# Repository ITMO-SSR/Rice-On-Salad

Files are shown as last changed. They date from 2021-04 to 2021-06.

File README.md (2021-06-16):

[English](README_EN.md)
# Rice-On-Salad
**Цель проекта:**
Разработать доступный для воспроизведения проект гусеничной платформы с возможностью удаленного управления через ПК 
и ориентации в пространстве через камеры.
****
**Описание:**
Полностью Open-Source проект с возможностью легкого повторения. Все детали для печати будут лежать в открытом доступе.
****
**Задачи проекта:**
- Разработать и собрать гусеничную платформу
- Подобрать необходимую электронику
- Реализовать удаленное управление платформой через ПК и смартфон
- Добавить автоматическое управление
****
**Желаемый результат:**
Получить полностью управляемую и самостоятельно ориентирующуюся в пространстве гусеничную платформу

***
# Установка ROS на Raspberry Pi
В данном разделе мы опишем процесс установки ROS на Raspberry Pi, а также расскажем о том, как подключить робота 
к своему компьютеру.

## Шаг 1.
Для работы Raspberry Pi требуется операционная система, которая хранится на карте microSD. 
В нашем проекте мы используем образ Ubuntu 16.04 с уже установленным ROS, 
который вы можете скачать по [ссылке](https://downloads.ubiquityrobotics.com/pi.html). 
Для записи образа на SD-карту вам потребуется программа [balenaEtcher](https://www.balena.io/etcher/).

## Шаг 2.
Для дальнейшей работы с Raspberry Pi вам нужно установить и настроить ROS на компьютере, 
с которого вы планируете подключаться к вашему роботу. 
Наиболее простой вариант — запустить образ Ubuntu с предустановленным ROS с помощью виртуальной машины.
1. Скачайте виртуальную машину [VirtualBox](https://www.virtualbox.org/wiki/Downloads) и установите её.
2. Скачайте образ Ubuntu по [ссылке](https://downloads.ubiquityrobotics.com/vm.html).
3. Разархивируйте файл, который вы скачали. В результате получится папка, внутри которой будет файл 
   с расширением `.vbox`. Запустите его. В результате откроется менеджер Virtual Box.
4. Проверьте параметры виртуальной машины и запустите её. Имя пользователя - `ubuntu`, пароль - `ubuntu`.

## Шаг 3.
Теперь, когда все необходимое ПО было установлено, рассмотрим процесс подключения к Raspberry Pi через SSH.
1. При первом включении Raspberry будет работать в режиме точки доступа Wi-Fi, к которой нужно будет подключиться 
   с вашего компьютера. Имя сети — `ubiquityrobotXXXX`, где `XXXX` - комбинация цифр. 
   Пароль для подключения - `robotseverywhere`.
2. После подключения к сети, откройте терминал в Ubuntu и введите команду `ssh ubuntu@10.42.0.1`. 
   Далее введите пароль `ubuntu`.
3. Для того чтобы в дальнейшем подключаться к роботу через вашу Wi-Fi сеть, нужно добавить её в список робота. 
   Для просмотра доступных сетей наберите команду `pifi list seen`. Для добавления вашей сети воспользуйтесь 
   командой `sudo pifi add MyNetwork password`, где `MyNetwork` и `password` - имя и пароль вашей сети. 
   Далее, введите `sudo reboot` в терминале. Это приведет к перезапуску робота, который теперь 
   будет автоматически подключаться к вашей сети.
4. Подключитесь к данной сети с вашего компьютера и снова откройте терминал Ubuntu. Теперь, чтобы подключиться к роботу, 
   воспользуйтесь командой `ssh ubuntu@address`, где `address` - IP-адрес вашего робота. Чтобы узнать его, 
   выполните следующие действия:
    1. Введите в терминале команду `ifconfig`. В ответ вы получите информацию по сетевым интерфейсам:
       
         ```
         eth0: flags=4099<UP,BROADCAST,MULTICAST>  mtu 1500
                 ether b8:27:eb:5b:d7:ae  txqueuelen 1000  (Ethernet)
                 RX packets 0  bytes 0 (0.0 B)
                 RX errors 0  dropped 0  overruns 0  frame 0
                 TX packets 0  bytes 0 (0.0 B)
                 TX errors 0  dropped 0 overruns 0  carrier 0  collisions 0
 
         lo: flags=73<UP,LOOPBACK,RUNNING>  mtu 65536
                 inet 127.0.0.1  netmask 255.0.0.0
                 inet6 ::1  prefixlen 128  scopeid 0x10<host>
                 loop  txqueuelen 1000  (Local Loopback)
                 RX packets 0  bytes 0 (0.0 B)
                 RX errors 0  dropped 0  overruns 0  frame 0
                 TX packets 0  bytes 0 (0.0 B)
                 TX errors 0  dropped 0 overruns 0  carrier 0  collisions 0
 
         wlan0: flags=4163<UP,BROADCAST,RUNNING,MULTICAST>  mtu 1500
                 inet 192.168.1.2  netmask 255.255.255.0  broadcast 192.168.1.255
                 inet6 fe80::1e3a:e952:1094:4fda  prefixlen 64  scopeid 0x20<link>
                 ether 00:e0:4c:06:6f:dc  txqueuelen 1000  (Ethernet)
                 RX packets 257  bytes 33734 (32.9 KiB)
                 RX errors 0  dropped 14  overruns 0  frame 0
                 TX packets 153  bytes 26653 (26.0 KiB)
                 TX errors 0  dropped 0 overruns 0  carrier 0  collisions 0
         ```           
       
       Обратите внимание на адрес `inet 192.168.1.2.`. IP-адрес Raspberry Pi будет иметь вид `192.168.1.x`, 
       где `x` - число от 1 до 255.
    2. Теперь, для того, чтобы найти адрес Raspberry Pi, можно воспользоваться 
       приложением [Advanced IP Scanner](https://www.advanced-ip-scanner.com). 
       Запустите приложение, введите `192.168.1.1-255` и нажмите "Сканировать". 
       В результате вы увидите список устройств, подключенных к вашей сети, среди которых будет и Raspberry.
5. Поздравляем! Вы подключились к своему роботу!

## Шаг 4.
Вполне вероятно, что в будущем вы захотите запускать часть нод на роботе, а часть на компьютере. 
Для этого настроим переменные среды.
1. Запустите виртуальную машину, откройте терминал и наберите следующие команды:
   
    ```
    echo "export ROS_MASTER_URI=http://<robot_ip>:11311" >> ~/.bashrc
    echo "export ROS_IP=$<workstation_ip>" >> ~/.bashrc
    ```
   
    где `<robot_ip>` и `<workstation_ip>` - IP-адреса робота и виртуальной машины соответственно.
2. Подключитесь к Raspberry Pi через SSH и наберите следующие команды:
   
    ```
    echo "export ROS_MASTER_URI=http://<robot_ip>:11311" >> ~/.bashrc
    echo "export ROS_IP=$<robot_ip>" >> ~/.bashrc
    ```

***
# Подключение шаговых двигателей к Arduino Uno с помощью CNC Shield
В данном разделе мы рассмотрим подключение шаговых двигателей к Arduino Uno, рассмотрим необходимые для этого 
компоненты и напишем небольшую тестовую программу.

## 1. Необходимые компоненты
1. CNC Shield v3.0
2. Arduino Uno
3. Драйверы A4988 - 2 шт.
4. Шаговые двигатели NEMA17 17HS4401 - 2 шт.
5. Шлейфы из 4 проводов для подключения шаговых двигателей - 2 шт.
6. USB-кабель для связи с компьютером

## 2. Соединение CNC Shield с Arduino Uno и драйверами
CNC Shield имеет четыре слота — для подключения четырех драйверов двигателей. Слоты, обозначенные желтым цветом, 
отвечают за оси X, Y, Z, красный слот — за ось A.

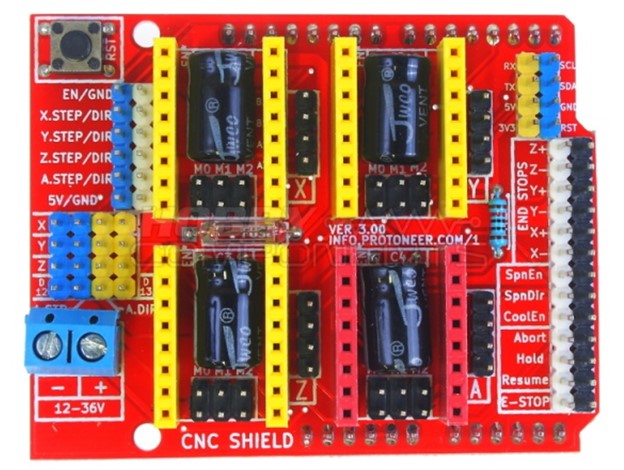
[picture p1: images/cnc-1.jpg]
CNC Shield 1


Ось A может дублировать одну из осей X, Y, Z с помощью дополнительного двигателя и драйвера. То есть входной сигнал 
приходит одинаковый, а драйверы и шаговые двигатели разные, но двигаются одинаково. В нашем случае 
дублирование осей не нужно, поэтому вставляем драйверы в 2 из 3 слотов X, Y, Z, а сам CNC Shield в Arduino Uno, 
как на картинке ниже.

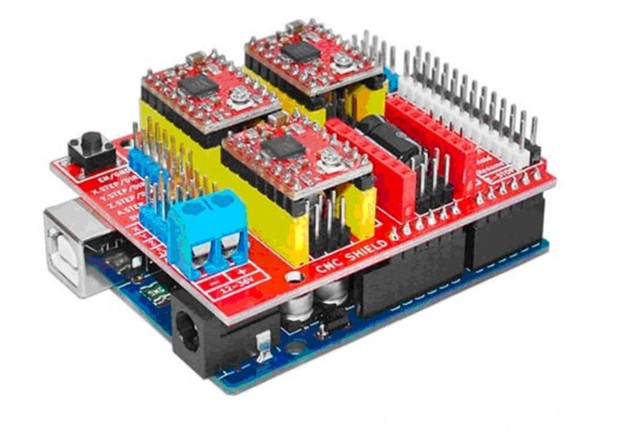
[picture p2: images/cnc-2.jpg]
CNC Shield 2


## 3. Настройка тока драйверов
Для настройки дополнительно потребуются отвертка и мультиметр.

Сначала подключим сборку плат к компьютеру по USB. Далее, включаем на мультиметре измерение постоянного напряжения 
напротив положения “20”. Для измерения напряжения необходимо приложить минусовой щуп к минусу на CNC Shield, 
а положительный щуп замкнуть с подстроечным резистором, который по совместительству является "+" в данной схеме. 
Необходимо вращать подстроечный резитор, пока мультиметр не покажет требуемое значение напряжения, 
при вращении по часовой стрелке, значения растут, против часовой стрелки — напряжение падает. 

Настройку расчетных значений необходимо повторить это для всех активных драйверов в сборке. В нашем случае 
мультиметр должен показать 1.01 В. 

Основные моменты процесса настройка показаны на рисунке ниже:

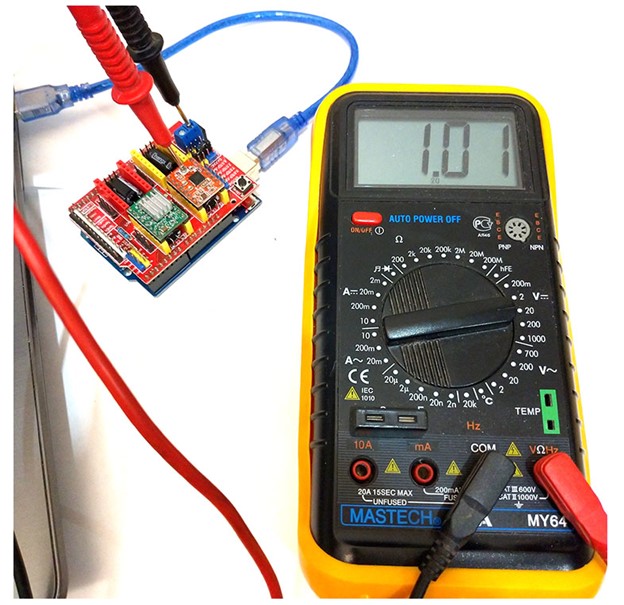
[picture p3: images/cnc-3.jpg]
CNC Shield 3


## 4. Подключение шаговых двигателей
Провода от шаговых двигателей подключаются последовательно в данный разъем:

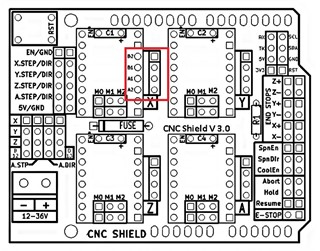
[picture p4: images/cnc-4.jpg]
CNC Shield 4


## 5. Распиновка при подключении CNC Shield
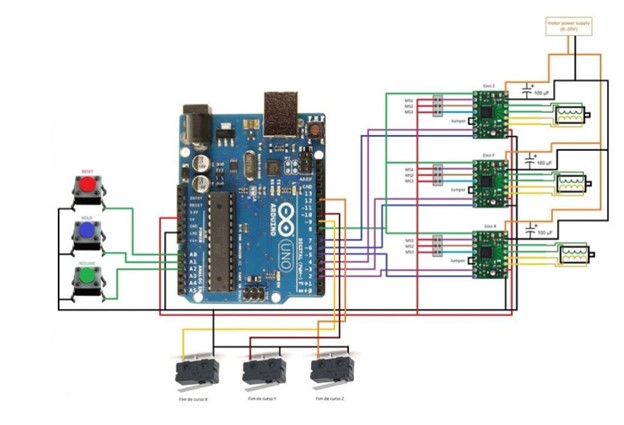
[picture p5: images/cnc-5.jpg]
CNC Shield 5

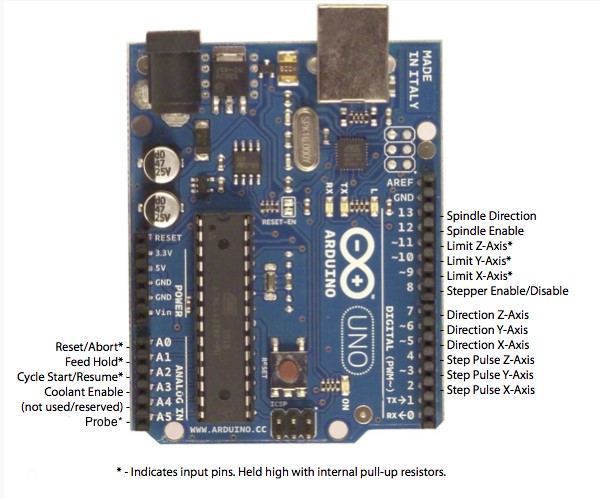
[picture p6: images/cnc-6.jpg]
CNC Shield 6


**Важно!** По умолчанию CNC Shield подает на 8 пин Stepper Enable/Disable высокий сигнал, который отключает драйвера, 
поэтому для их работы в программе необходимо прописать следующие строчки:

```
pinMode(8, OUTPUT);
difitalWrite(8, LOW);
```

Также мы можем подавать высокий сигнал на 8 пин, чтобы отключить режим удержания позиции двигателями, 
когда не нужно двигаться, чтобы не тратить лишнюю энергию. Главное — не забыть включить их перед началом движения.

## 6. Библиотека AccelStepper
Для управления шаговыми двигателями мы используем библиотеку AccelStepper.

Установка библиотеки:
1. Скачиваем библиотеку с [сайта](http://www.airspayce.com/mikem/arduino/AccelStepper/index.html)
2. Скачанный zip архив добавляем в Arduino IDE следующим образом:
   
    Скетч > Подключить Библиотеку > Добавить .ZIP библиотеку  > выбираем скачанный архив > open

Использование библиотеки:
1. подключение библиотеки
`#include <AccelStepper.h>`

2. подключения шагового двигателя через драйвер(согласно распиновки):
   
    ```
    AccelStepper Xaxis(1, 2, 5);
    AccelStepper Yaxis(1, 3, 6);
    AccelStepper Zaxis(1, 4, 7);
    ```

3. Установка максимальной скорости:
`Xaxis.setMaxSpeed(stepsPerSecond);`

4. Установка максимального ускорения:
`Xaxis.setMaxAcceleration(stepsPerSecondSquared);`

5. Переместиться в абсолютно указанное положение. Само движение запускается функцией run():
`Xaxis.moveTo(targetPosition);`

6. Переместиться в относительно указанное положение. Само движение запускается функцией run():
`Xaxis.move(distance);`

7. Вернуть текущее абсолютное положение:
`Xaxis.currentPosition();`

8. Вернуть расстояние до указанного положения:
`Xaxis.distanceToGo();`

9. Начать движение. Для продолжения движения следует вызвать функцию повторно:
`Xaxis.run();`

10. Начать движение и подождать, когда двигатель достигнет указанной точки. Функция не осуществляет возврата, пока двигатель не остановится:
`Xaxis.runToPosition();`

11. Установить скорость в шагах в секунду. Само движение запускается функцией runSpeed():
`Xaxis.setSpeed(stepsPerSecond);`

12. Начать движение. Для продолжения движения следует вызвать функцию повторно:
`Xaxis.runSpeed();`

## 7. Тестовая программа
```
#include <AccelStepper.h> //подключение библиотеки

//установка двигателей
AccelStepper Xaxis(1, 2, 5); // pin 2 = step, pin 5 = direction
AccelStepper Yaxis(1, 3, 6); // pin 3 = step, pin 6 = direction

void setup() {
  //включение драйверов
  pinMode(8, OUTPUT);
  digitalWrite(8, LOW);
  //установка максимальной скорости
  Xaxis.setMaxSpeed(1000);
  Yaxis.setMaxSpeed(1000);
  //установка скорости движения
  Xaxis.setSpeed(500);
  Yaxis.setSpeed(-800);
}

void loop() {
   //запуск двигателей с заданной скоростью  
   Xaxis.runSpeed();
   Yaxis.runSpeed();
}
```

***
# История разработки гусеницы
**Начальная задача:** придумать оптимальные гусеницы для робоплатформы.  
**Основные параметры:**
 - Ширина гусеницы 
 - Расстояние между центрами вращения траков.  

Если касаемо ширины трака все было довольно однозначно: берем среднее соотношение ширины траков и корпуса у вездеходов 
средней весовой категории, что составило 0.67 (сумма ширины траков к ширине корпуса без учета траков), то есть 
при заданной ширине 150 мм ширина каждого трака составила 50 мм.

Длина трака подбиралась под диаметр ведущего колеса, в чем очень помог Советский учебник по расчету гусеничных шасси 
(“Расчет и конструирование гусеничных машин Н.А. Носова издательство “Машиностроение” Ленинград 1972”).

После определения параметров пришло время определиться с зацеплением.  

В первом прототипе использовалось захождение 2 в 3 ушка, однако от этого было решено отказаться из-за большого масштаба 
и недостаточного разрешения FDM 3D печати.  

Вторым прототипом было зацепление 1 в 2 ушка, которое и было выбрано для дальнейшей работы.

Кроме того, был переработан паз для зацепления с ведущим катком.

Для первой версии были использованы квадратные окна, повторяющие профиль зуба в серединном сечении, которые 
не обеспечивали достаточного захождения зацепного зуба на колесе в трак, а так же обеспечивали слишком 
малый контакт зацепления, что могло привести к прокручиванию и разуванию гусеницы.

Для второго прототипа были выбраны торчащие по бокам гусеницы штыри, которые размещались в полость между зубцами колеса, 
что обеспечивает отличный контакт и хорошее вхождение в зацепление. Таким образом, 2 версия уже является хорошим траком 
из-за легкости, прочности, воспроизводимости на FDM принтере и зацепляемости проволкой от 0.8 до 1.2 мм в диаметре.

К 3-м тракам 2-й версии было напечатано 24 трака 3-й версии для оценки соединений на большом количестве траков, а так же 
общей гибкости и упругости гусеничного полотна.

Дальнейшие изменения трака лишь вносили небольшие коррективы. Третий прототип немногим отличается от второго. Было 
добавлено 2 отверстия в траке, которые в дальнейшем позволят дооснащать гусеничное полотно различными грунтозацепами, 
повышая приспособленность гусеницы под различные условия без необходимости изготовления новой.

Четвертой и финальной версией был закрыт вопрос с препятствованием разуванию и оптимальному взаимодействию 
с опорными катками. Было добавлено два зуба толщиной по 1.5 мм на расстоянии 19 мм, что при печати из PETG пластика 
обеспечивает достаточную прочность для сопротивления к поперечным нагрузкам и размещению и прокатыванию между ними 
опорного катка шириной 18.8 мм.  

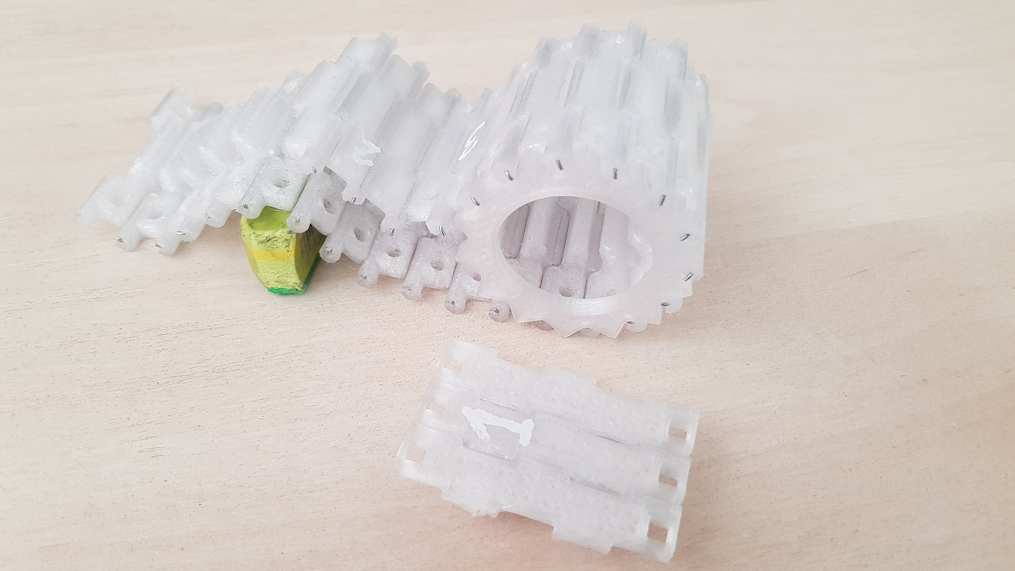
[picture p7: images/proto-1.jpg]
Prototype 1

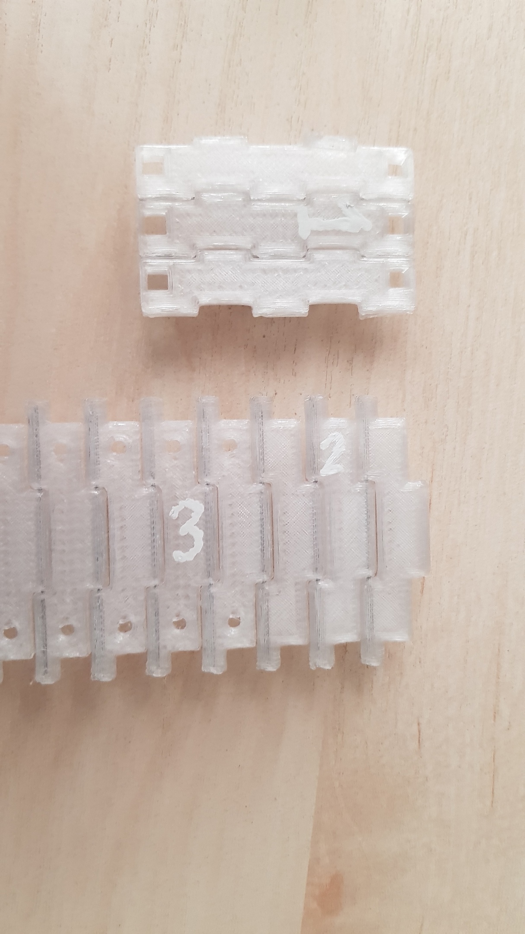
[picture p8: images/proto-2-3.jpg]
Prototype 2&3

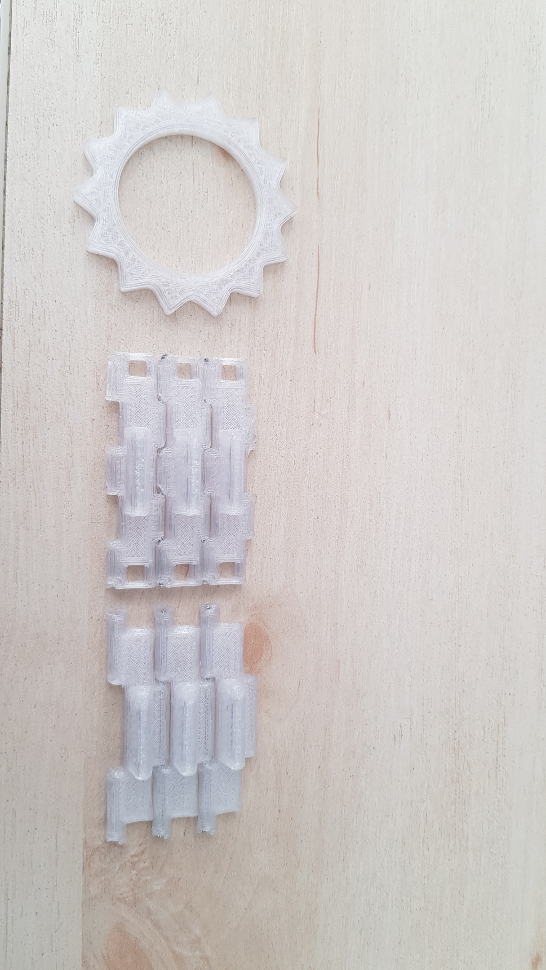
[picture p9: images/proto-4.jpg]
Prototype 4


***

# Компоновка
При создании какой-либо сложной системы первоочередной и основополагающей задачей должна быть компоновка элементов.

При решении этой задачи необходимо четко понимать:
 - Какие элементы будут в системе 
 - Способы их воздействия на систему 
 - Массу (для некоторых случаев)  

Так как в начале разработки нашего робота не было четкого понимания того, какие элементы нужны, какие моторы 
будут использоваться, модель создавалась с запасом.

Когда уже был готов корпус, рассчитан гусеничной движитель и продумана подвеска, появилось представление 
о начинке нашего дрона. Первоначально задумывалось использование 2-х легких бк двигателей для приведения системы 
в рабочее положение, которые должны были располагаться в передней части корпуса. Собственно под них был спроектирован 
специальный отсек.

Однако, позже, для решения задачи точного позиционирования нашей системы был осуществлен переход на шаговые двигатели, 
которые были больше и тяжелее первоначально выбранных. В корпусе пришлось сделать пропилы, а двигатели слишком сильно 
перемещали центр масс дрона вперед. При разгоне это даже хорошо, ведь корпус не кренило назад, но при торможении 
вся система стремилась перевернуться, несмотря на внушительный противовес в кормовой части дрона.

Также для гостиничного движителя не так благоприятно размещение ведущего колеса спереди, нежели сзади. Вот почему 
ведущий каток, расположенный в кормовой части натягивает полотно гусеницы со стороны поверхности по которой едет, 
при движении в основном направлении-вперед. Если ведущее колесо расположено спереди, то при движении вперед оно 
натягивает полотно гусеницы по верхней части движителя и стремится протолкнуть гусеницу вниз между 
опорными катками и поверхностью, что может повлечь за собой холостое проворачивание ведущего колеса 
при слабом натяжении гусеницы. Также расположение ведущего колеса сзади позволяет разместить двигатели в кормовой части. 
Это позволит нивелировать опрокидывающий момент при резком торможении.

В конечном итоге мы разместили шаговые двигатели и ведущие колеса в задней части дрона, что позволило лучше реализовать 
работу подвески.

Теперь основная масса находится в кормовой части, хоть и дрон не переворачивается необходимо сместить центр тяжести 
как можно ближе к центру дрона. Мы установили аккумулятор и все управляющие элементы максимально близко к передней части, 
теперь наша конструкция не переворачивается и максимально эффективно реализует работу гусеничного движителя.

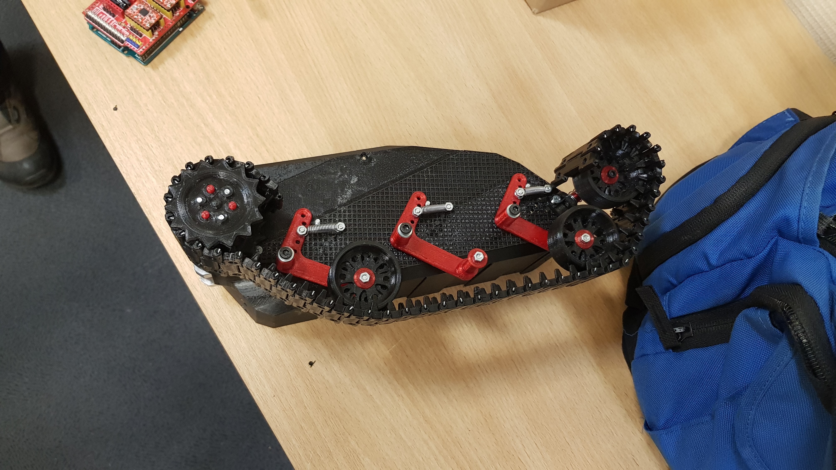
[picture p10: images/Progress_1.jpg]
Progress 1

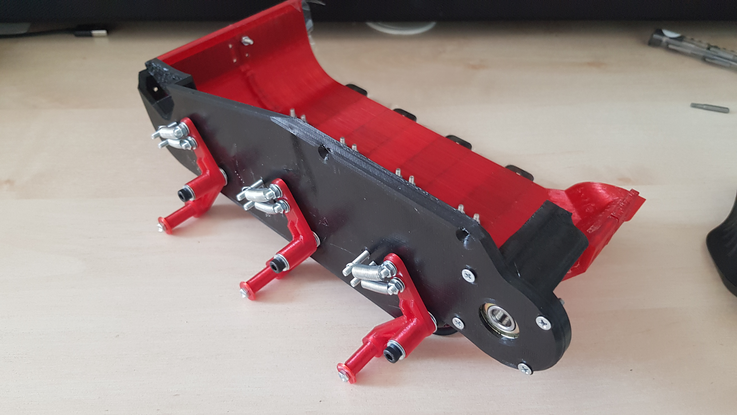
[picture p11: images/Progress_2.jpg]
Progress 2

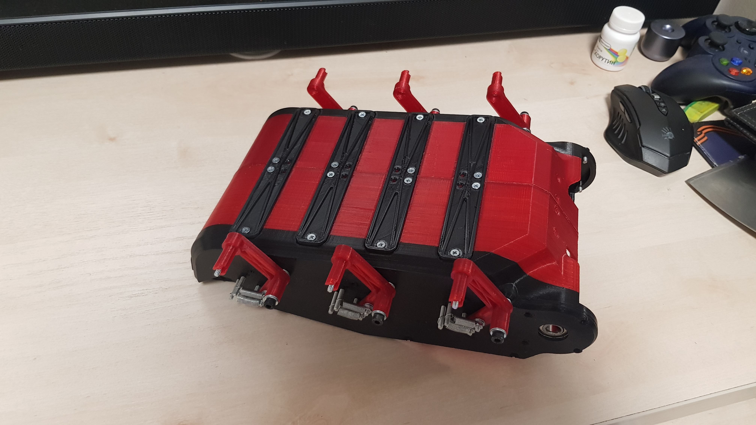
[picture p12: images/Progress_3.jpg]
Progress 3

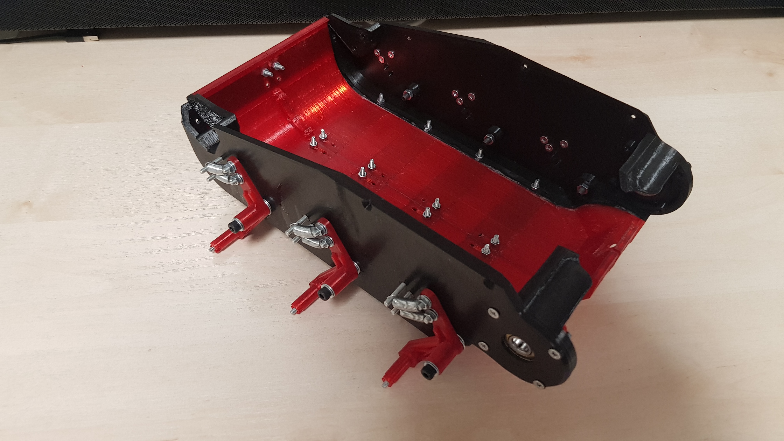
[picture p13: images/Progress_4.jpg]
Progress 4

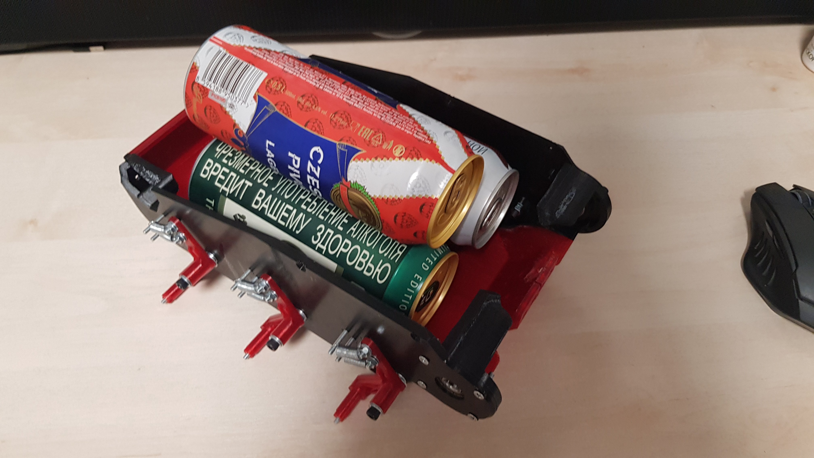
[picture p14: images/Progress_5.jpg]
Progress 5

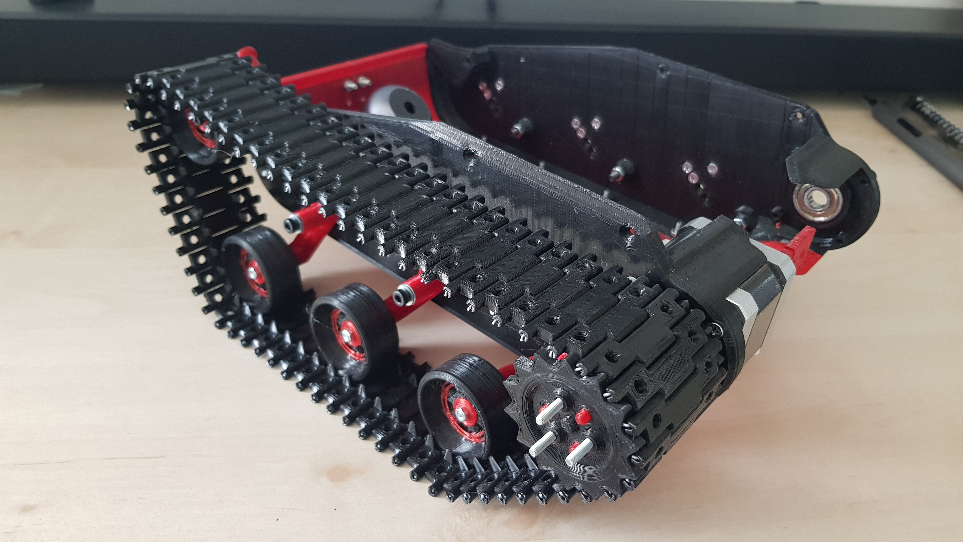
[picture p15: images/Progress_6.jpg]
Progress 6

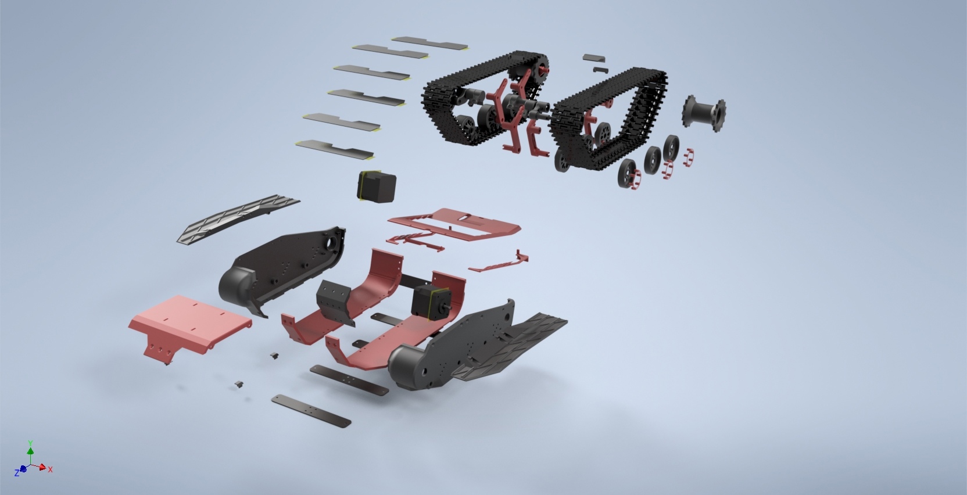
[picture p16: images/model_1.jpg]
Model 1

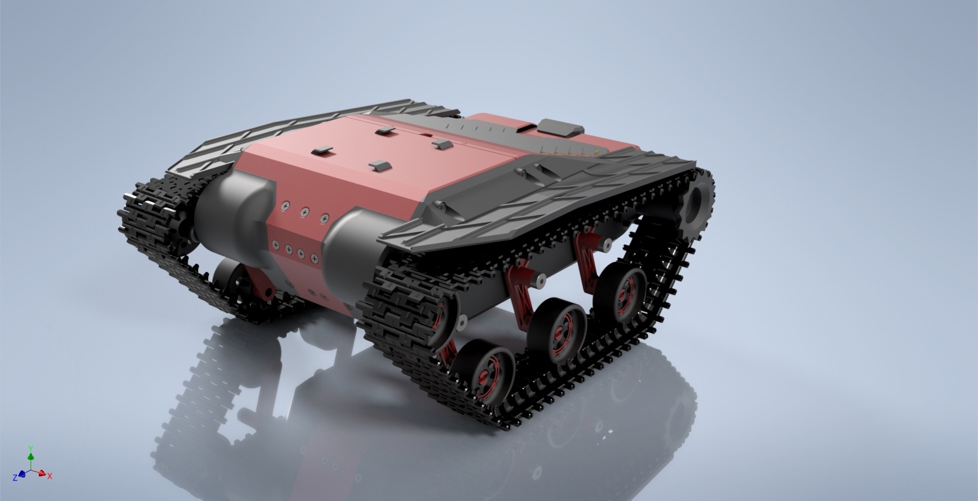
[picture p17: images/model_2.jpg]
Model 2

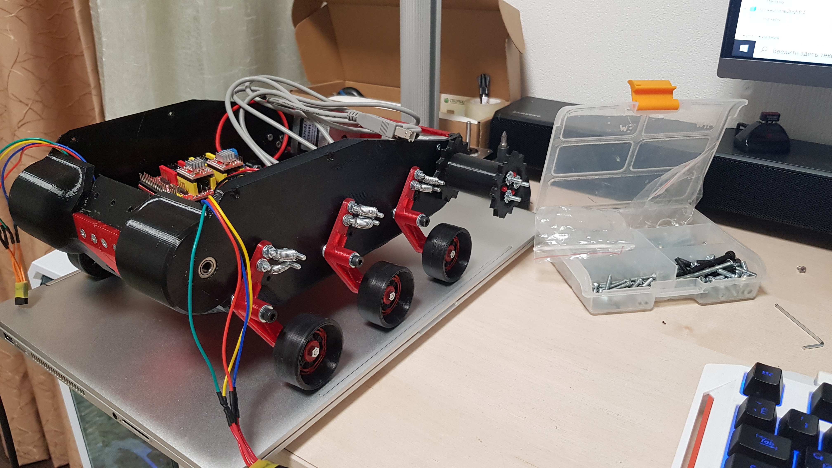
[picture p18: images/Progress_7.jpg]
Progress 7

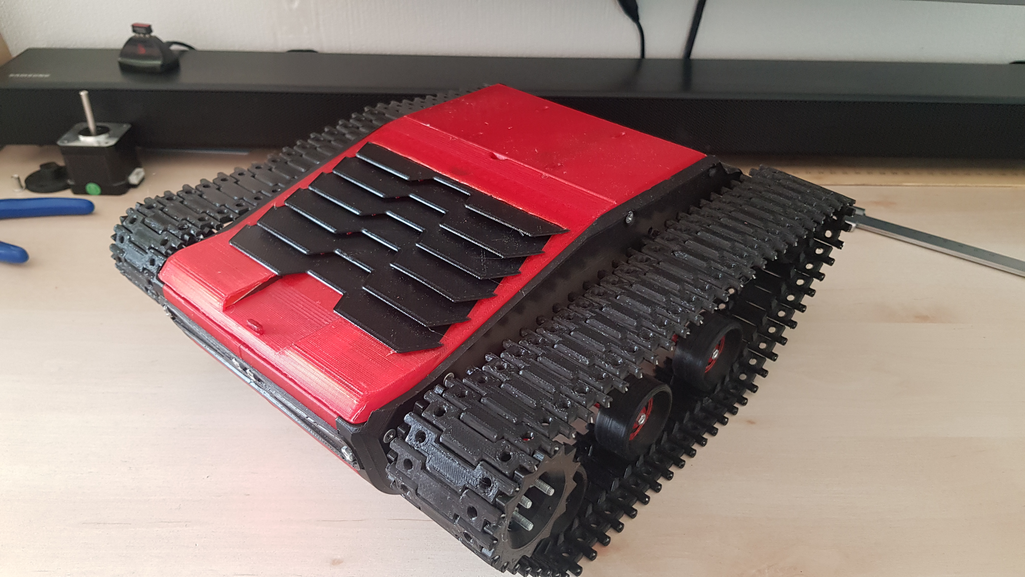
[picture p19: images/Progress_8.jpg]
Progress 8

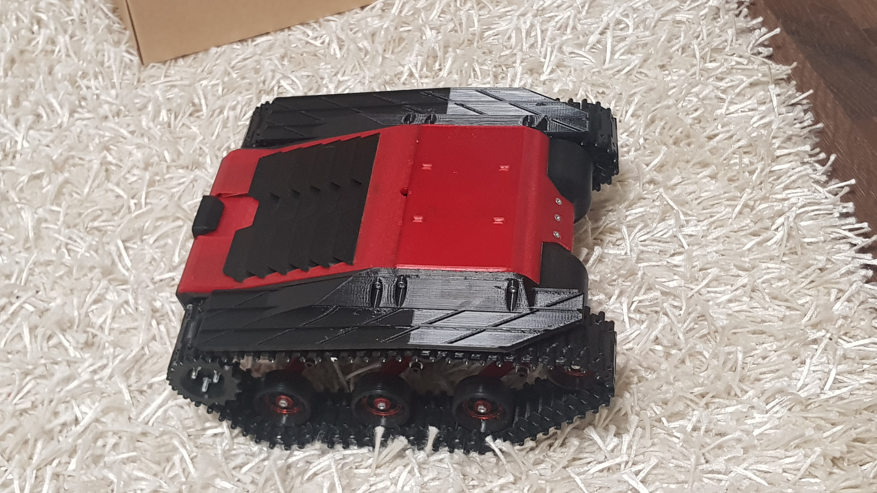
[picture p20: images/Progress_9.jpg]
Progress 9

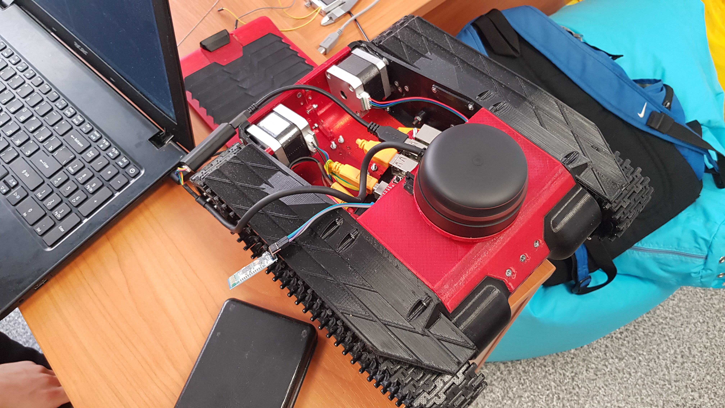
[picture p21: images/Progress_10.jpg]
Progress 10


***
# Управление роботом с клавиатуры
В данном разделе мы расскажем, как подключить Raspberry Pi к Arduino через UART-интерфейс, а также напишем программу 
для управления роботом с помощью клавиатуры.

Для начала необходимо активировать UART на Raspberry Pi. Для этого подключитесь к микрокомпьютеру через SSH и наберите 
в терминале команду `sudo nano /boot/config.txt`. В открывшемся файле добавьте в конец строку `enable_uart=1`. Далее, 
выполните ребут с помощью команды `sudo reboot`, чтобы изменения вступили в силу.

Теперь нужно определить имя Arduino при подключении через USB. Наберите в терминале `ls /dev/tty*`. Вы увидите 
список адресов. Сделайте скриншот (он пригодится, чтобы найти адрес Arduino). После этого подключите Arduino к 
Raspberry Pi через USB и снова наберите эту команду. В списке должен появиться новый адрес, соответствующий Arduino 
(в нашем случае этот адрес имел вид `/dev/ttyACM0`). Запомните его, он пригодится нам при написании программы.

Приступим к написанию управляющей программы.

Начнем с создания узла ROS, который будет считывать нажатия на клавиши и передавать их Arduino для управления двигателями.

```
$ cd ~/catkin_ws/src
$ catkin_create_pkg control_node rospy geometry_msgs.msg
```

Последняя команда создаст новый ROS-пакет с названием `control_node` и зависимостями `rospy` и `geometry_msgs`.
Далее, наберите:

```
$ cd control_node
$ mkdir scripts
$ cd scripts
$ nano control_node.py
``` 

В результате откроется редактор.
Наберите в нем код из [данного файла](programs/ros/control_node.py). Учтите, что в `arduino_name` должен быть адрес, 
полученный вами ранее. После этого, выполните:

```
$ chmod +x control_node.py
$ ~/catkin_ws
$ catkin_make
```

В результате все пакеты в catkin_workspace будут собраны и готовы к запуску.

Теперь напишем скетч для Arduino. Подключите Arduino к вашему компьютеру, откройте Arduino IDE и создайте программу 
с содержанием из [этого файла](programs/arduino/sketch_keyboard_control.ino).

Осталось протестировать нашу программу. Запустите программу на Arduino и подключитесь к Raspberry Pi через USB. 
Затем откройте второй терминал. В одном из них наберите `rosrun control_node control_node.py` - эта команда запустит 
написанный нами узел. В другом наберите `rosrun teleop_twist_keyboard teleop_twist_keyboard.py`.

На экране должно появиться следующее:

```
Reading from the keyboard  and Publishing to Twist!
---------------------------
Moving around:
   u    i    o
   j    k    l
   m    ,    .

For Holonomic mode (strafing), hold down the shift key:
---------------------------
   U    I    O
   J    K    L
   M    <    >

t : up (+z)
b : down (-z)

anything else : stop

q/z : increase/decrease max speeds by 10%
w/x : increase/decrease only linear speed by 10%
e/c : increase/decrease only angular speed by 10%

CTRL-C to quit
```

Теперь при нажатии на одну из клавиш выше робот начнет двигаться.

Поздравляем! Вы успешно написали программу для управления роботом с клавиатуры!

# Управление роботом со смартфона
В данном разделе мы рассмотрим управление роботом с использованием мобильного приложения.

## Шаг 1. Установка дробления шага
Для установки необходимого дробления шага установим перемычки на пины под драйверами. В нашем случае установим 1/8 шага,
вставляя перемычки в MS0 и MS1. Теперь 1 шаг в программе будет равен 8-ой части от полного шага, соответственно, нужно 
увеличить значения скоростей в 8 раз.

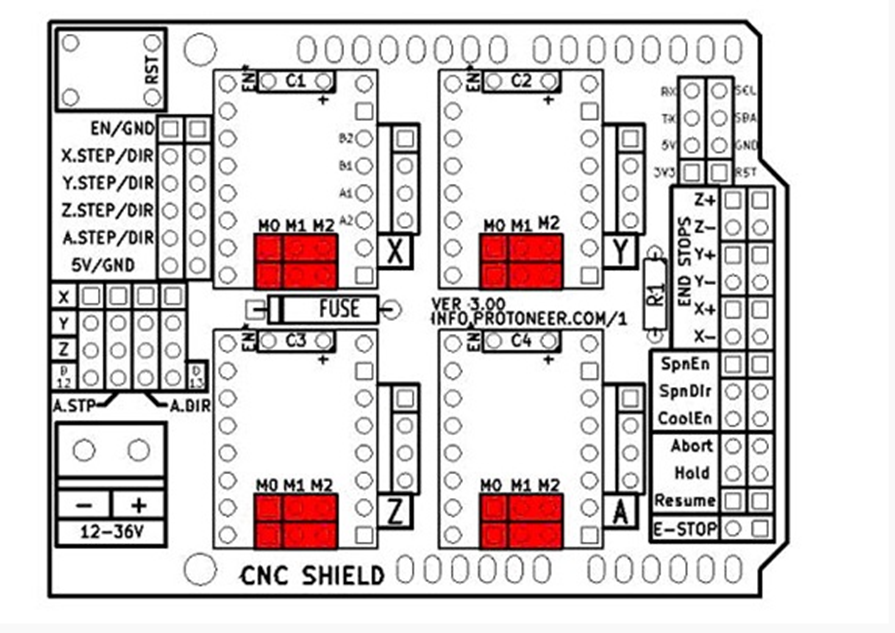
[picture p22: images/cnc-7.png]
CNC Shield 7

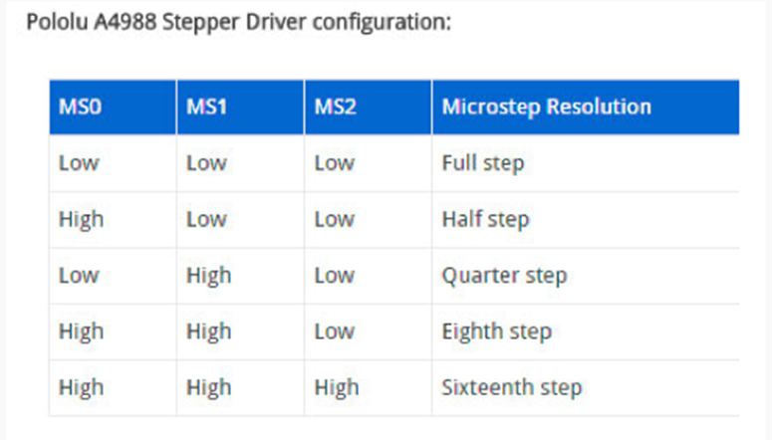
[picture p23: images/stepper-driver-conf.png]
Stepper Driver Configuration


## Шаг 2. Подключение Bluetooth-модуля
Для подключения Bluetooth-модуля воспользуемся местом для установки драйвера ось Z.
 - белый — земля
 - светло-серый — 5 В
 - серый — rx Arduino tx модуля
 - жёлтый — tx Arduino rx модуля

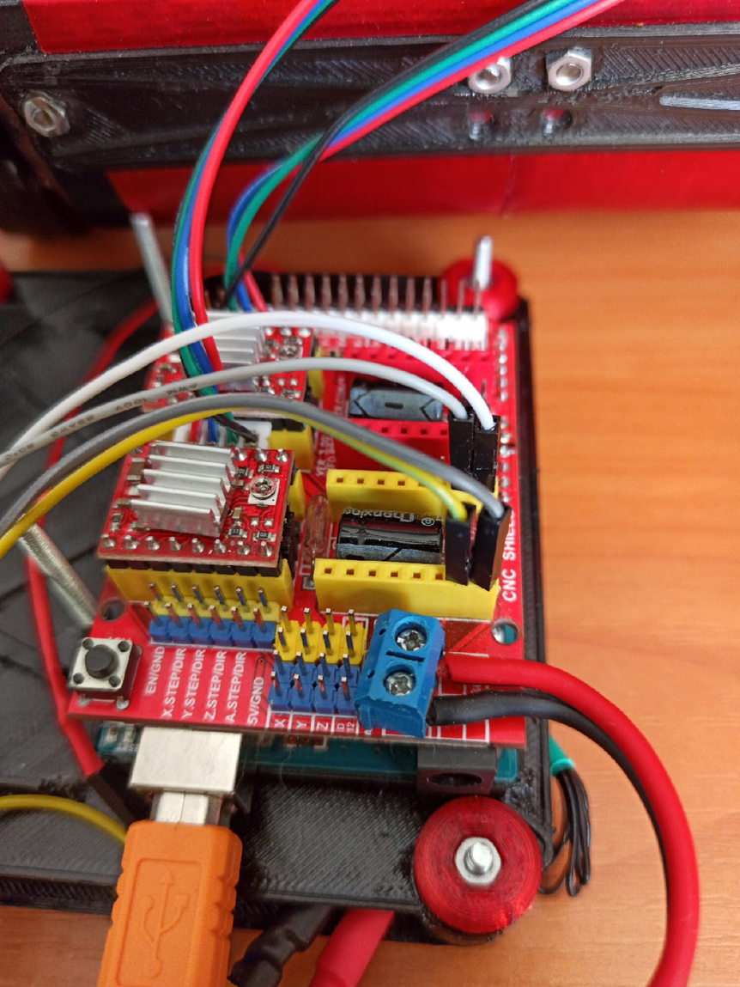
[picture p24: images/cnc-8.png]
CNC Shield 8


## Шаг 3. Полезные ссылки
 - https://3dtoday.ru/blogs/xedos/sandbox-cnc-shield-v30-iron/
 - http://cnc-design.ru/sborka-arduino-uno-i-cnc-sheild-v3.html
 - https://3d-diy.ru/wiki/arduino-moduli/bluetooth-modul-hc-05/
 - https://hobbytech.com.ua/arduino-библиотека-accelstepper-для-шагового-двигател/

## Шаг 4. Мобильное приложение
Для дистанционного управления нашим роботом будем использовать мобильное приложение 
[Arduino Joystick](https://play.google.com/store/apps/details?id=uncia.robotics.joystick&hl=ru&gl=US).

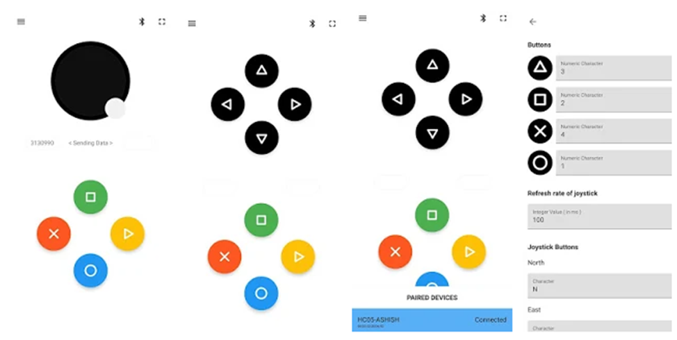
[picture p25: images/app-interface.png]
App Interface


После установки приложения необходимо подключиться к роботу для это сперва включите Bluetooth и добавить робота в 
сопряженные устройства. Имя - `RC-Caterpillar` (по умолчанию `HC-05`), пароль - `3317` (по умолчанию `0000` или `1234`).
Далее, в приложении нажимаем на иконку Bluetooth и выбираем нашего робота. 

Теперь, отклоняя джойстик, мы можем задавать скорость и направление движения нашего робота, а с помощью 3 кнопок 
(красная, синяя и желтая) задавать скоростные режимы роботу, а с помощью зеленой включать и выключать режим остановки 
перед препятствиями.

При необходимости в приложении доступна документация и некоторые настройки.

## Шаг 5. Остановка перед препятствиями
Для определения расстояния до ближайшего препятствия воспользуемся лидаром.

Сначала подключимся к Raspberry Pi через SSH.

Затем установим пакет rplidar_ros, который будет обрабатывать полученные с лидара данные и публиковать их 
в топик `\scan`:

```
$ cd ~/catkin_ws/src
$ git clone https://github.com/Slamtec/rplidar_ros.git
```

Далее, создадим новый пакет, который будет обрабатывать сообщения с лидара и передавать сигнал об остановке на Arduino:
```
$ catkin_create_pkg distance_node rospy sensor_msgs.msg
$ cd distance_node
$ mkdir scripts
$ cd scripts
$ nano distance_node.py
```

В открывшемся редакторе наберите код из [файла](programs/ros/distance_node.py). Далее,

```
$ chmod +x distance_node.py
$ cd ~/catkin_ws
$ catkin_make
$ source devel/setup.bash
```

Запустим наши программы. В первом терминале наберем `roslaunch rplidar_ros rplidar.launch`, во втором - 
`rosrun distance_node distance_node.py`.

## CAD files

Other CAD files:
model/RCP-2.0.iam
model/ВедущееКолесо V2.ipt
model/ВедущееКолесо.ipt
model/ВедущееКолесоВнутр.ipt
model/ВерхнийКрюк.ipt
model/ВнешНат.ipt
model/ВнешНатПр.ipt
model/ВнешНатяжитель.ipt
model/ВнешНатяжительПр.ipt
model/ВнутрНат.ipt
model/ВнутрНатПр.ipt
model/ВнутрНатяжитель.ipt
model/ВнутрНатяжительПР.ipt
model/Втулка.ipt
model/Держатель каскада.ipt
model/Держатель каскада2.ipt
model/Зажим проводов.ipt
model/Корпус внутр.ipt
model/Корпус внутр2.ipt
model/Корпус.ipt
model/Корпус4.ipt
model/Крепление лидара.ipt
model/Крепление плат.ipt
model/Крепление пружины.ipt
model/Крышка.ipt
model/Муфта2.ipt
model/Надкрылок.ipt
model/НадкрылокПравый.ipt
model/Направляющая1.ipt
model/ОпорныйКаток.ipt
model/ОпорныйКаток2.ipt
model/Перед-верх.ipt
model/Пластина.ipt
model/Подпорный.ipt
model/ПодпорныйКаток.ipt
model/Потшипник.ipt
model/РеброСкрепления.ipt
model/РельсКрышки.ipt
model/РучкаКрышки.ipt
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

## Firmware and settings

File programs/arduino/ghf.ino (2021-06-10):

#include <AccelStepper.h> //подключаем библиотеку AccelStepper
#include<SoftwareSerial.h>
//указываем к каким пинам подключен драйвер с шаговым двигателем
AccelStepper LeftStepper(1, 2, 5); // pin 2 = step, pin 5 = direction
AccelStepper RightStepper(1, 3, 6); // pin 3 = step, pin 6 = direction

//Создаем необходимые переменные
int Lspeed; //Скорость левого двигателя шагов/секунду
int Rspeed; //Скорость правого двигателя шагов/скунду
String data = "0000000";//Получаемая с телефона команда
String dataPrev;//Предыдущая полученная с телефона команда
bool zero;//маркер остановки
int button = 2;//Нажатая кнопка на телефоне по умолчанию 2
int power = 0;//Скорость полученная с телефона
int angle;//Угол, полученный с телефона
String block = "0";//Команда с пишки для остановки/замедления перед препятствием
long comand;//Числовое значение команды с телефона
bool stop_mode = false;//Маокер активации режима остановки перед препятствием

//Задаем лимиты скорости на различные режимы
int limit1 = 3000;//Для 1 режима
int limit2 = 6000;//Для 2 режима
int limit3 = 9000;//ДЛЯ 3 режима

int limit = limit2;//Задаем режим работы по умолчанию

int minlim = 200;//устанавливаем минимальную скорость

SoftwareSerial Bluetooth(4,7);//Показываем к каким пинам подключен Bluetooth модуль

void setup() {
  Serial.begin(9600);//Запускаем Serial для получения команд с пишки
  pinMode(8, OUTPUT); //Устанавливаем режим работы 8 пина, отвечающего за включение/отключение драйверов, на выход
  LeftStepper.setMaxSpeed(12000); //устанавливаем максимальную скорость левого шагового двигателя шагов/секунду
  LeftStepper.setAcceleration(7000); //устанавливаем максимальное ускорени левого шагового двигателя шагов/секунду в квадрате
  RightStepper.setMaxSpeed(12000); //устанавливаем максимальную скорость правого шагового двигателя шагов/секунду
  RightStepper.setAcceleration(7000); //устанавливаем максимальное ускорени правого шагового двигателя шагов/секунду в квадрате
  digitalWrite(8, LOW); //Подаем сигнал низкого уровня на 8 пин для включения драйверов
  Bluetooth.begin(38400); //Открываем канал предачи данных для получения команд с телефона
  Bluetooth.setTimeout(1);//Устанавливает timeOut времени чтения данных с канала
  zero = false;//Начальный маркер остановки false
  Lspeed = 0; //Задаем начальное значение скорости левого двигателя
  Rspeed = 0; //Задаем начальное значение скорости правого двигателя
  LeftStepper.setSpeed(Lspeed);//устанавливаем рассчитанную скорость на левый двигаетль
  RightStepper.setSpeed(Rspeed);//устанавливаем рассчитанную скорость на правый двигаетль
}

void loop() {
  if(stop_mode){//если режим остановки перед препятствием активирован
    if (Serial.available()>0){//если есть данные с пишики
      block = Serial.readStringUntil('#');//считываем их до спец символа
      if(((block=="1")&&(angle<=180))||((block=="2")&&(angle>180))){//Если получена информации по пути движения приравниваем скорости к 0
        Lspeed = 0;
        Rspeed = 0;
      }
      if(block=="0"){//если получена команда об удалении от препятсвия на нужное расстояние или исчезновения препятствия
        limit = speedMode(button);//восстанавливаем режим скорости
        if (power!=0){//если мы остановились из-за препятствия 
          calcSpeed(power, angle, limit);//возобновляем движение
        }
      }
      if(block == "4"){//если получена информации о приближении к препятствию
        limit = limit1;//переходит на минимальный режим скорости
        calcSpeed(power, angle, limit);//пересчиваем скорость в связи с изменением режима
      }
      LeftStepper.setSpeed(Lspeed);//устанавливаем рассчитанную скорость на левый двигатель
      RightStepper.setSpeed(Rspeed);//устанавливаем рассчитанную скорость на правый двигатель
    }
  }
  if (Bluetooth.available()>0){//если еть доступные данные то начинаем их прием и обработку
    data = Bluetooth.readStringUntil('#');//считваем данные из канала как строку
    if((data.length()==7)&&(dataPrev!=data)){//Если команда получена полностью и она не равна предыдущей
      dataPrev = data;//запоминаем команду
      comand = data.toInt();//переводим ее в long
      angle = comand/10000;//Выделяем угол 
      power = (comand%10000)/10;//Выделяем скорость
      if(comand%10==4){//Если нажата кнопка активации/деактивации режима остановки
        stop_mode = !stop_mode;//включаем/выключаем режим остановки
        block = "0";//задаем блок по умолчанию 0 - препятствий нет
      }else if((comand%10!=0)&&(block=="0")){//если нажата кнопка изменения режима скорости и препятствий нет
        button = comand%10;//запоминаем режим
        limit = speedMode(button);//задаем предел
      }
      if((comand/10==0)||((block=="1")&&(angle<=180))||((block=="2")&&(angle>180))){//если получена команда об остановке или о движении в препятсвие останавливаемся
        Lspeed = 0;
        Rspeed = 0;
      }else{//в ином случаем
        calcSpeed(power, angle, limit);//расчитываем скорости согласно полученой команде
      }
      LeftStepper.setSpeed(Lspeed);//устанавливаем рассчитанную скорость на левый двигатель
      RightStepper.setSpeed(Rspeed);//устанавливаем рассчитанную скорость на правый двигатель
    }
  }
  if (!zero){//если маркер остановки не активирован то запускаем двигатели с установленной скоростью
    LeftStepper.runSpeed();//запускаем левый двигатель
    RightStepper.runSpeed();//запускаем правый двигатель
  }
  if(Lspeed==0&&Rspeed==0&&!zero){//если получена команда остановки и маркер остановки еще не установлен
    zero=true;//включаем маркер остановки
    digitalWrite(8, HIGH);//отключаем драйвера
  }
}

//функция для изменения режима скорости соответсвенно нужной кнопке задает нужный режим
int speedMode(int mode){
  if(mode==1){
    return limit1;
  }else if(mode==2){
    return limit2;
  }else if(mode==3){
    return limit3;
  }
}


//Функция расчета скоростей для двигателей
void calcSpeed(int p, double a, int lim){
  p = map(p, 0, 100, minlim, lim);//пресчитываем силу от 0 до 100 в от нижнего до верхнего предела
  double ar = a/180*M_PI;//переводим угол в радианы
  if(a<=90){//если джостик в первой четверти
    Lspeed = p;//подаем полную скорость на левый трак
    Rspeed = trunc(p*sin(ar));//скорость для правого умножаем на синус угла и отбрасываем дробную часть
  }else if(a<=180){
    Rspeed = p;//подаем полную скорость на правый трак
    Lspeed = trunc(p*sin(ar));//скорость для левого умножаем на синус угла и отбрасываем дробную часть
  }else if(a<=270){
    Rspeed = -p;//подаем полную скорость умноженную на -1 на правый трак
    Lspeed = trunc(p*sin(ar));//скорость для правого умножаем на синус угла и отбрасываем дробную часть
  }else if(a<=360){
    Lspeed = -p;//подаем полную скорость умноженную на -1 на левый трак
    Rspeed = trunc(p*sin(ar));//скорость для левого умножаем на синус угла и отбрасываем дробную часть
  }
  if (zero){//если был активен маркер остановки
    zero=false;//выключаем маркер остановки
    digitalWrite(8, LOW);//включаем драйвера
  }
}

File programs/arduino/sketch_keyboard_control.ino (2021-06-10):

#include <AccelStepper.h>

AccelStepper LeftStepper(1, 2, 5); // pin 2 = step, pin 5 = direction
AccelStepper RightStepper(1, 3, 6); // pin 3 = step, pin 6 = direction

int Lspeed;
int Rspeed;
long comand;
boolean PiSignal;
boolean zero;
int flag;
String data;

void setup() {
  pinMode(8, OUTPUT);
  pinMode(4, INPUT);
  LeftStepper.setMaxSpeed(1000);
  LeftStepper.setAcceleration(5000);
  RightStepper.setMaxSpeed(1000);
  RightStepper.setAcceleration(5000);
  digitalWrite(8, LOW);
  Serial.begin(9600);
  flag = 0;
  zero = false;
  Lspeed = 0;
  Rspeed = 0;
  data  = "10000000";
}

void loop() {
  //PiSignal = digitalRead(4)==HIGH;
  //if(!PiSignal){
    //if(flag==0){
      //flag=1;
      //LeftStepper.setSpeed(0);
      //RightStepper.setSpeed(0);
      //LeftStepper.runSpeed();
      //RightStepper.runSpeed();
      //digitalWrite(8, HIGH);
    //}
  //}else{
    //if(flag==1){
      //flag=0;
      //digitalWrite(8, LOW);
    //}
    if (Serial.available()>0){
      String data = Serial.readStringUntil('\n');
      comand = data.toInt();
      //Serial.println(comand);
      Lspeed = calculateSpeed(comand/10000);
      Rspeed = calculateSpeed(comand%10000);
      LeftStepper.setSpeed(Lspeed);
      RightStepper.setSpeed(Rspeed);
    }
    if (!zero){
      LeftStepper.runSpeed();
      RightStepper.runSpeed();
    }
    if(Lspeed==0&&Rspeed==0){
      zero=true;
      digitalWrite(8, HIGH);
    }else if(zero){
      zero=false;
      digitalWrite(8, LOW);
      LeftStepper.setSpeed(Lspeed);
      RightStepper.setSpeed(Rspeed);
      LeftStepper.runSpeed();
      RightStepper.runSpeed();
    }
  }
//}

int calculateSpeed(long x)
{
  if (x/1000==1){
    return map(x%1000, 0, 100, 0, 1000);
  }else{
    return map(x%1000, 0, 100, 0, -1000);
  }
}

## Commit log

2021-03-05 Локализировал README под EN
2021-03-05 Внес небольшие исправления
2021-03-12 Добавил описание гусениц
2021-03-12 Added Track Development Stages to README_EN
2021-04-02 Программа для проверки работы
2021-04-09 Arduino programs
2021-04-23 Added a tutorial about connection motors to CNC Shield
2021-06-03 Moved Track Part
2021-06-10 Moved arduino sketches to programs/arduino
2021-06-10 Added arduino program
2021-06-16 added models
    [RCP-2.0.iam, ВедущееКолесо V2.ipt, ВедущееКолесо.ipt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]
